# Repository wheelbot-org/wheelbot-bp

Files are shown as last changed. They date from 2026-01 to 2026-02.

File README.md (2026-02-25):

# Чертежи и 3D модели проекта wheelbot

В папке `fcstd` лежат чертежи деталей в формате FreeCAD. Каждый файл - отдельная деталь. В папке `3mf` лежат уже подготовленные для 3D печати модели. Имена файлов в папках совпадают, отличаются только разрешения.

Все чертежи адаптированы под использование подшипников от роликовых коньков - стандарт 608 (8x22x7 mm), внутренний диаметр 8 mm. Выбор обусловлен их распрастраненностью и ценой. Установка подшипников в детали предполагается запресовкой (с натягом).

Для разъемных соединений используются винты M4 цилиндрический с внутренним шестигранником и гайки к ним. Выбор обусловлен их распрастраненностью, ценой, потребностью многократной сборки и разборки, скрытие шляпки.

Список не печатных деталей по [ссылке](./EXTERNAL-PARTS.md).

## Базовые узлы

### Рама

Рама с ребрами жесткости (изгиб, кручение) - 100x200 mm, для того, чтобы деталь помещалась на столы базовых 3D принтереров. На раме сеткой 25x25 mm размещены отверстия под винты с пазами для скрытия шляпки, на обратной стороне пазы для запресовки гаек.

|  Код | Название | Описание | Файл | Превью |
|---|---|---|---|---|
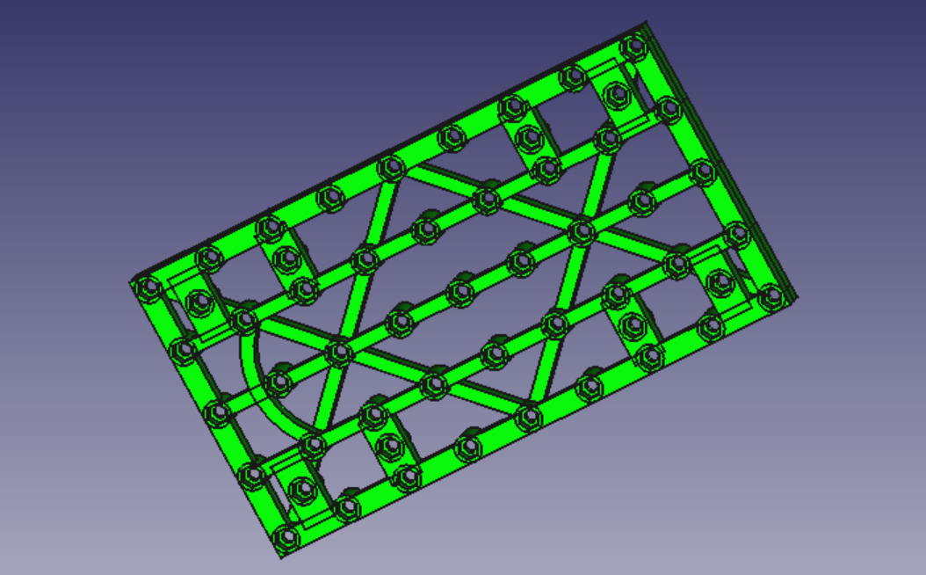
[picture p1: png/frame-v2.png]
| F.01 | Рама | Четыре площадки для крепления узлов мотор-редукторов. Одна площадка для крепления рулевого механизма на сервоприводе. | `frame-v2` |  |

### Рулевой узел

Рулевой механизим на основе сервопривода.

| Код | Название | Описание | Файл | Превью |
|---|---|---|---|---|
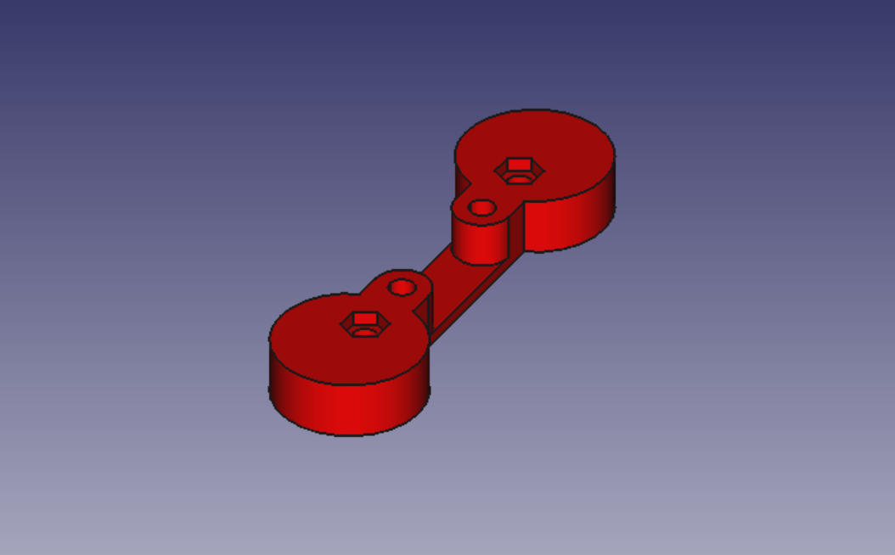
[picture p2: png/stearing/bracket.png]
| S.01 | Кронштейн-проставка | Для крепления к раме. | `stearing/bracket` |  |
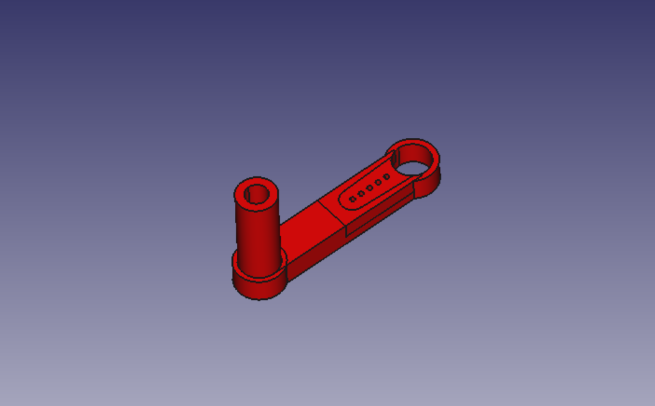
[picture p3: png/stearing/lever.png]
| S.02 | Рулевой рычаг | Передает усилие от сервопривода на центральный шатун. | `stearing/lever` |  |
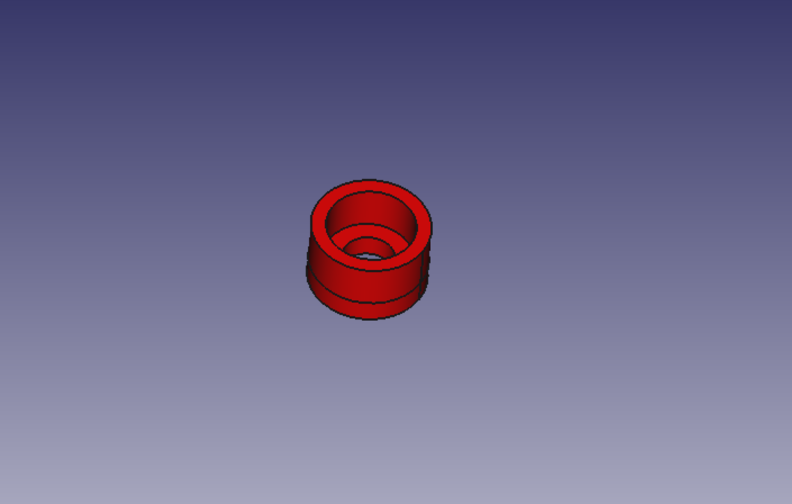
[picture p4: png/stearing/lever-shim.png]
| S.03 | Прокладки | Прокладка фиксации центрального шатуна на рулевом рычаге и боковых шатунах. Для сборки узла требуется три. | `stearing/lever-shim` |   |
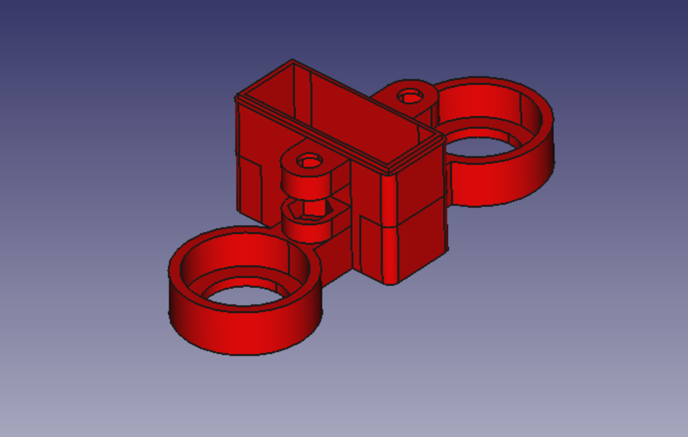
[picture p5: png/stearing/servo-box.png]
| S.04 | Корпус | Сервопривод размещается внутрь детали. Подшипники запресовываются. | `stearing/servo-box` |  |
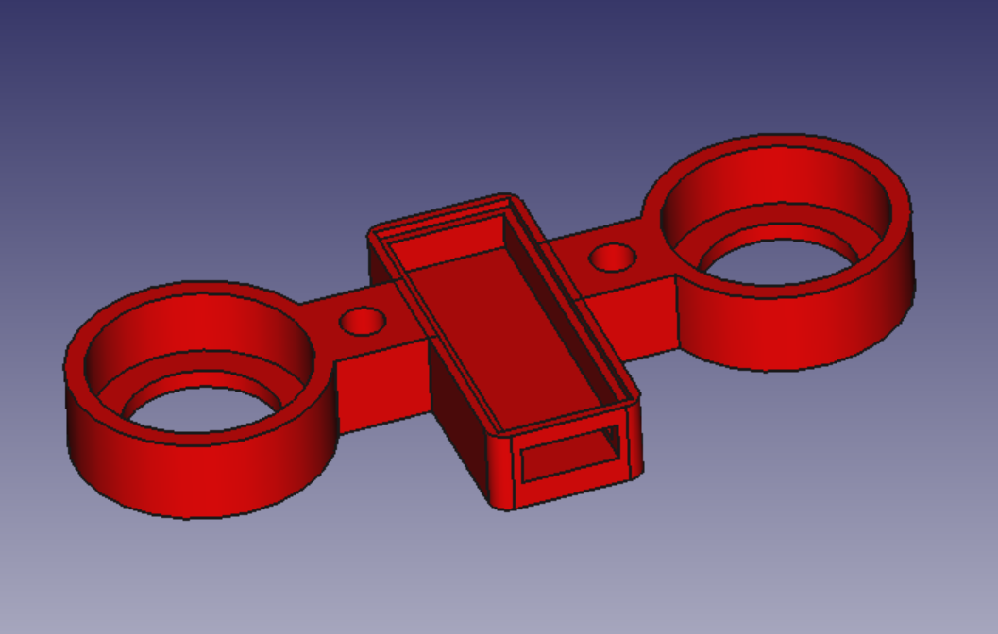
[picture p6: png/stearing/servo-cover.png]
| S.05 | Крышка | Подшипники запресовываются. | `stearing/servo-cover` |  |
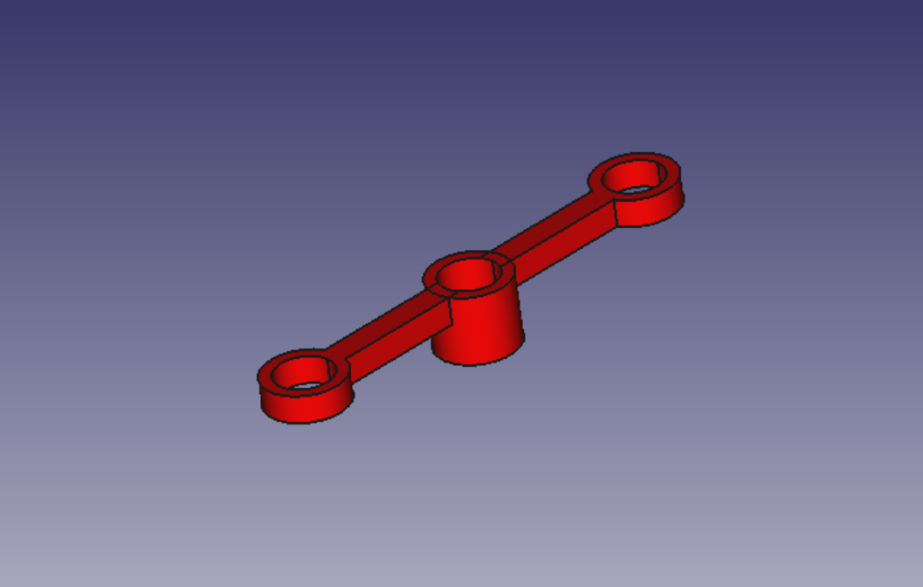
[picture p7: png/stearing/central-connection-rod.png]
| S.06 | Центральный шатун | Передает усилие на боковые шатуны. | `stearing/central-connection-rod` |  |
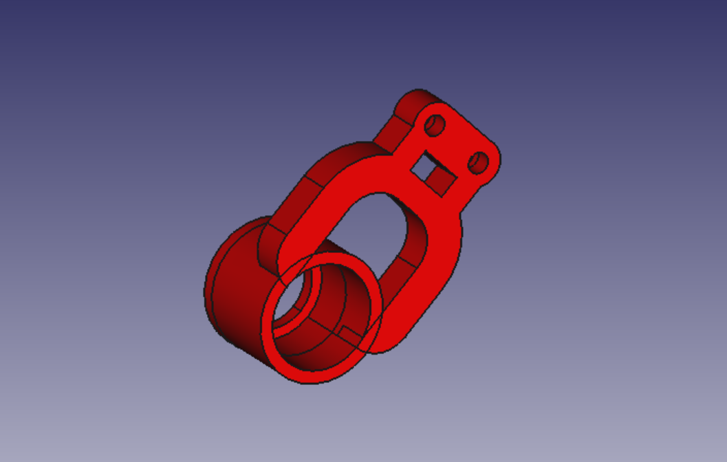
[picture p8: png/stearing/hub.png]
| S.07 | Ступицы | Для сборки узла требуется две. Деталь симетричная, зеркально отображать не нужно. | `stearing/hub` |  |
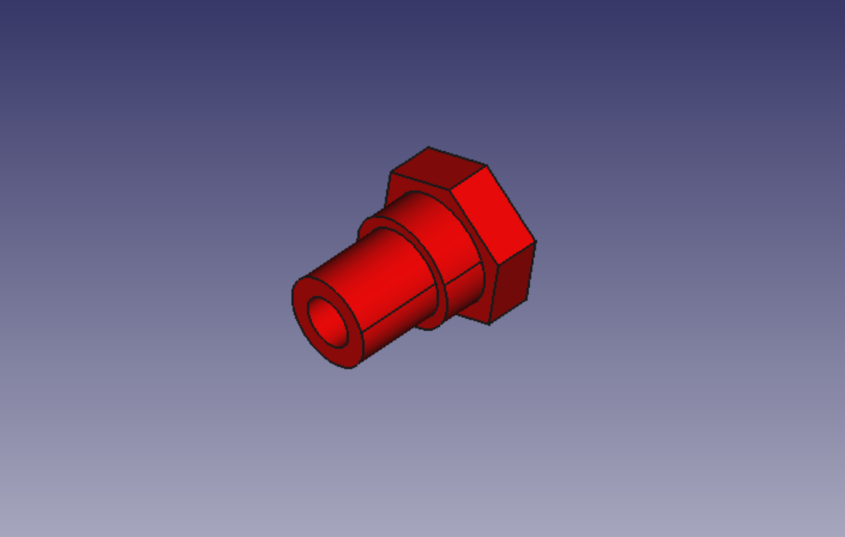
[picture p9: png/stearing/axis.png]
| S.08 | Оси | Оси для крепления дисков. Для сборки узла требуется две. | `stearing/axis` |  |
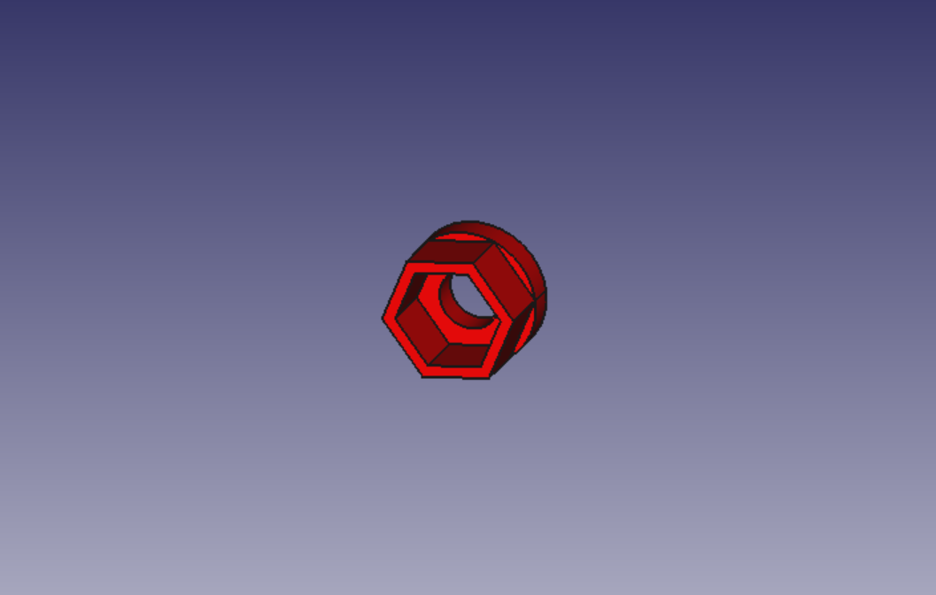
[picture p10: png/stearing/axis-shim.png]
| S.09 | Фиксаторы осей | Прокладки для фиксации подшипников к осям. Для сборки узла требуется две. | `stearing/axis-shim` |  |
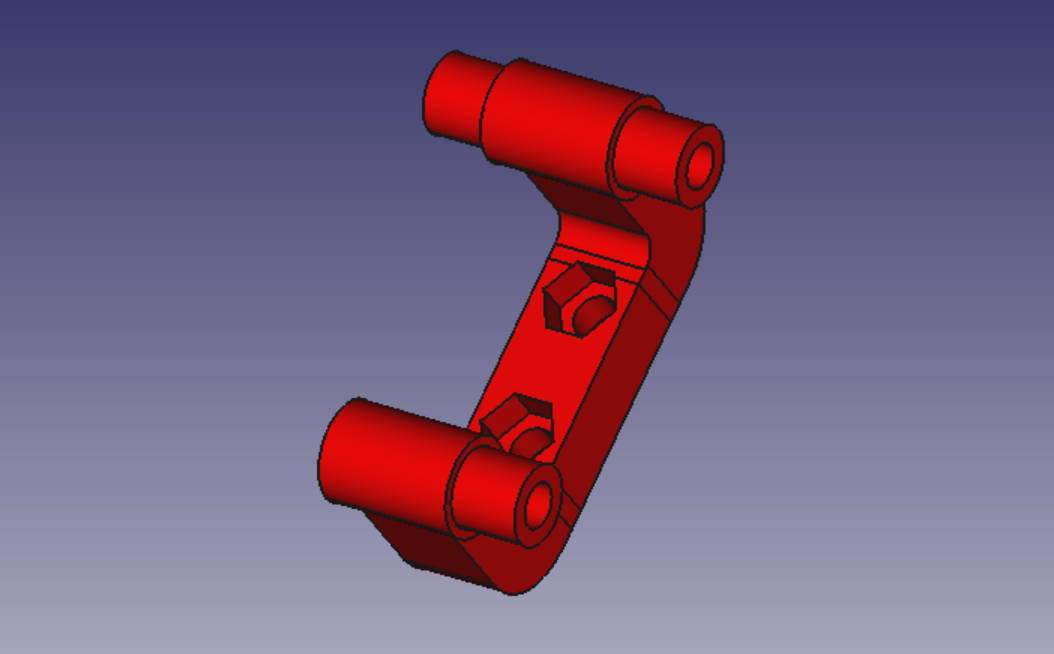
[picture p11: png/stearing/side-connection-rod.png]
| S.10 | Боковые шатуны | Передают усилие от центрального шатуна на ступицы. Для сборки узла требуется две, вторую требуется отобразить зеркально при печати. | `stearing/side-connection-rod` |  |

### Ходовой узел

Ходовые узлы построенные на мотор редукторах (DC3-6V TT). Минимум нужно два, при построении ровера без рулевого узла - четыре.

| Код | Название | Описание | Файл | Превью |
|---|---|---|---|---|
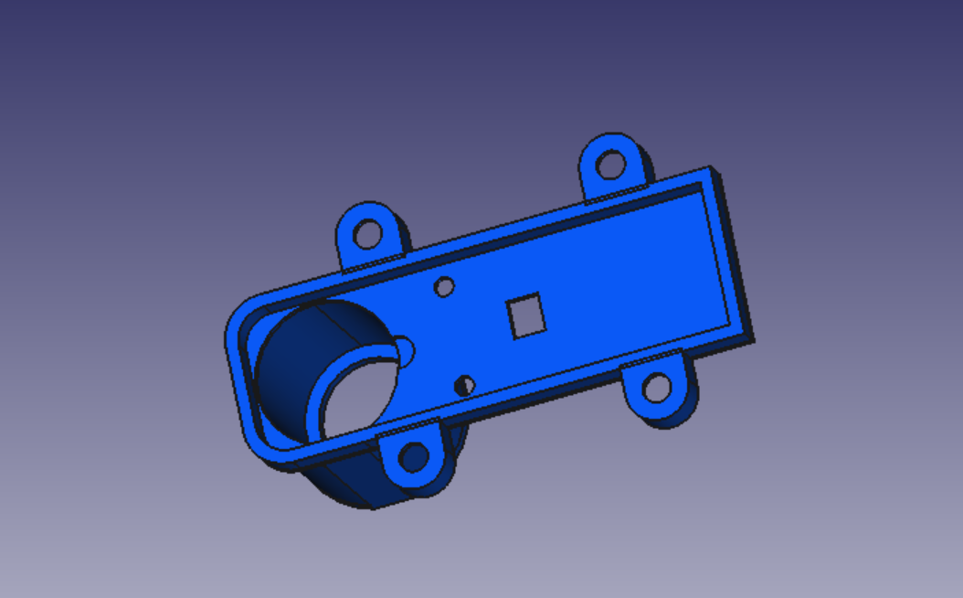
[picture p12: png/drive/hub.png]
| M.01 | Ступицы | - | `drive/hub` |  |
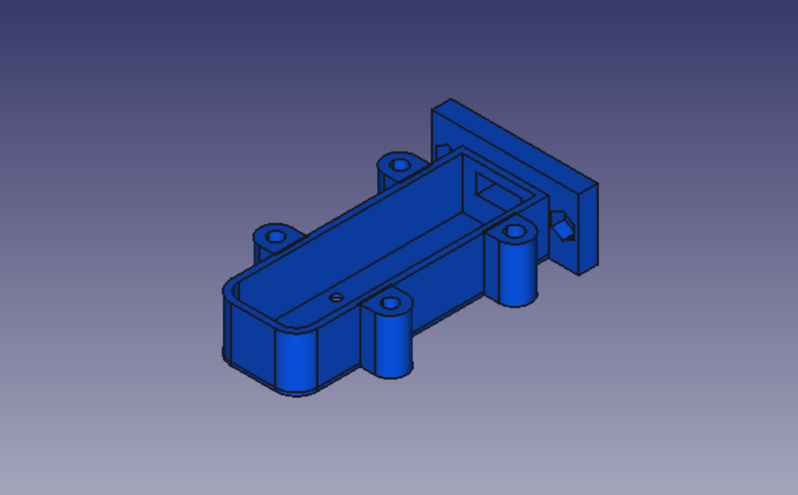
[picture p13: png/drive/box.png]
| M.02 | Корпус | Корпус для мотор-редуктора. | `drive/box` |  |
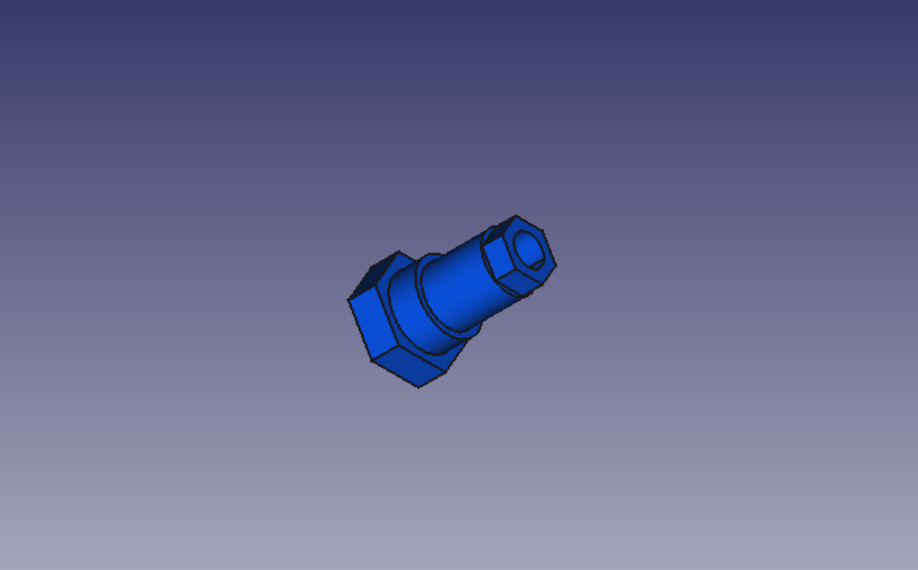
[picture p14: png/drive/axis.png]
| M.03 | Ось | - | `drive/axis` |  |
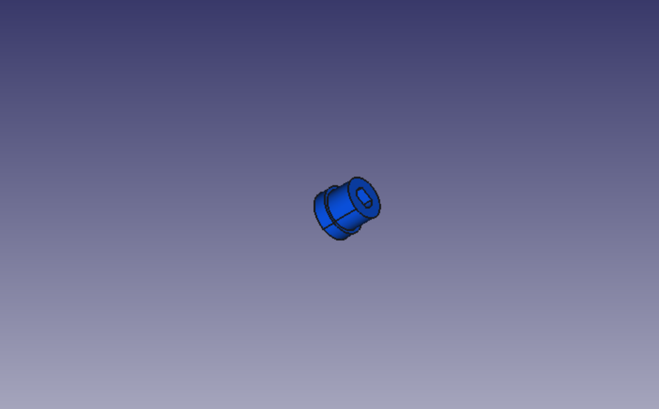
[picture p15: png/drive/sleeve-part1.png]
| M.04 | Муфта 1 | Муфта со стороны мотор-редуктора | `drive/sleeve-part1` |  |
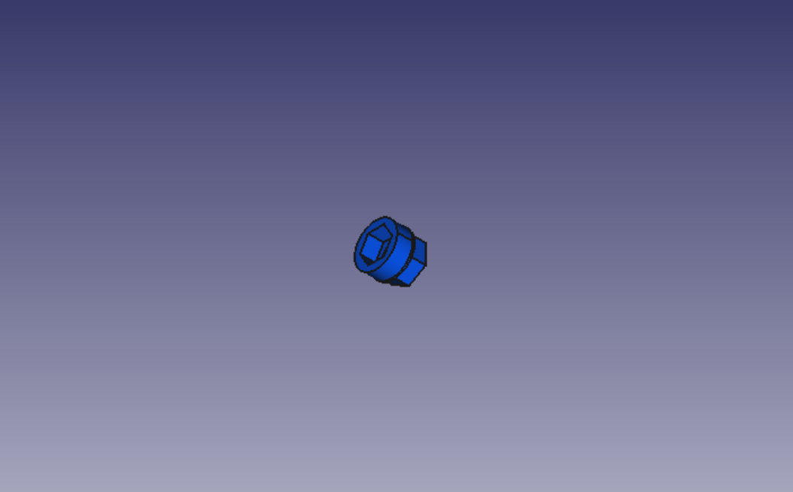
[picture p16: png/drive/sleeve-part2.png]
| M.05 | Муфта 2 | Муфта со стороны колеса | `drive/sleeve-part2` |  |

### Колесо

| Код | Название | Описание | Файл | Превью |
|---|---|---|---|---|
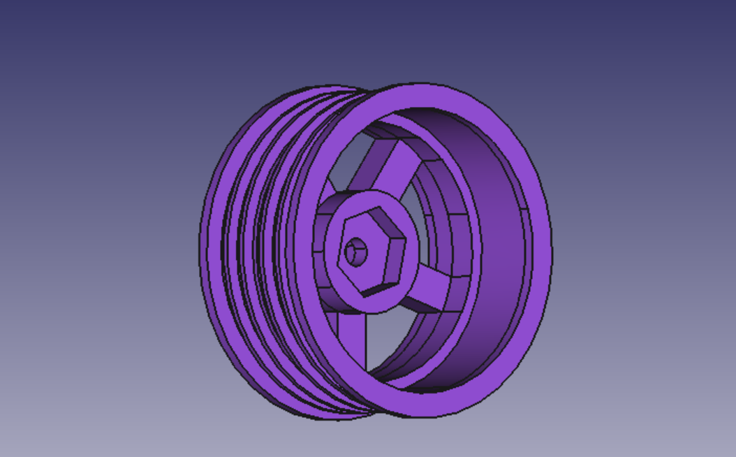
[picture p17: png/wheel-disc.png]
| W.01 | Диск | Диск для колес под покрышку для моделирования (RCAWD 1/10 63mm). Ребра на внешней стороне - необходимый элемент. | `wheel-disc` |  |

### Главный контроллер

Корпус под ESP8266 (NodeMCU), Drivers Shield.

| Код | Название | Описание | Файл | Превью |
|---|---|---|---|---|
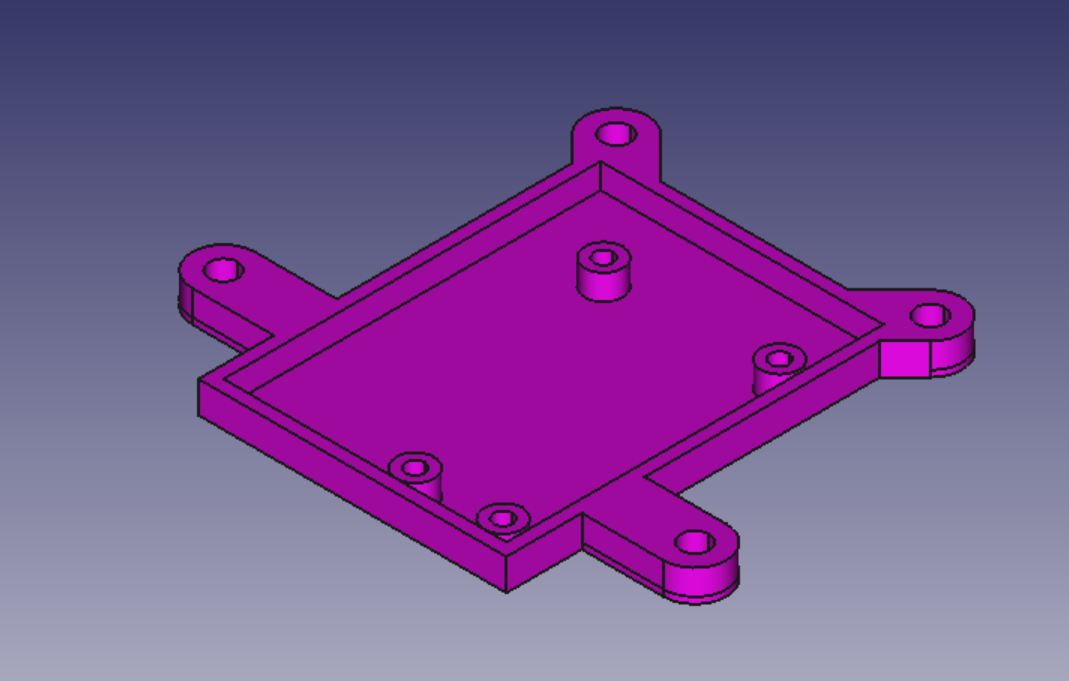
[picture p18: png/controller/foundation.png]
| MC.01 | Основание | - | `controller/foundation` |  |
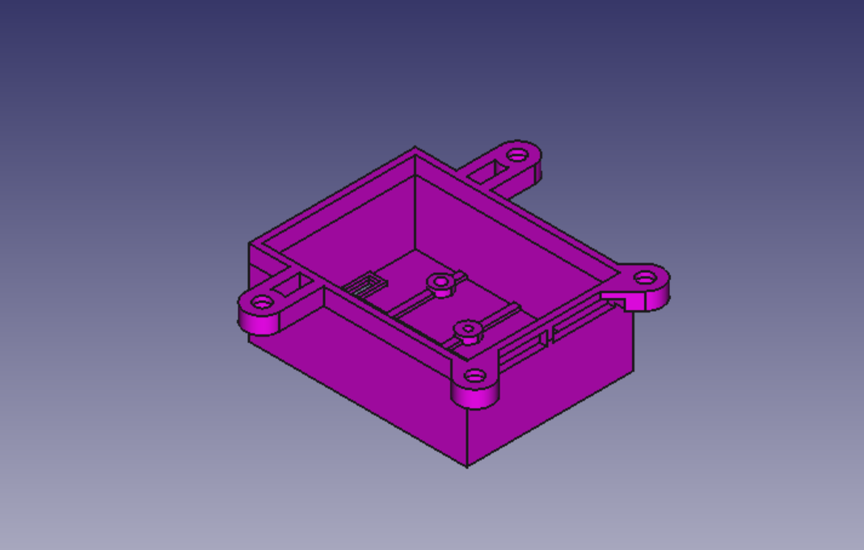
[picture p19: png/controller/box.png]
| MC.02 | Корпус | - | `controller/box` |  |

### Аккумуляторный блок

Корпус для крепления на раму батарейного отсека (ABS 18650 4x). Выполнен в 2х вариациях под BMS платы Balance и Enhance. Во всех вариантах предусмотрено крепление для ina226 и dc-dc преобразователя для питания 5 вольт.

| Код | Название | Описание | Файл | Превью |
|---|---|---|---|---|
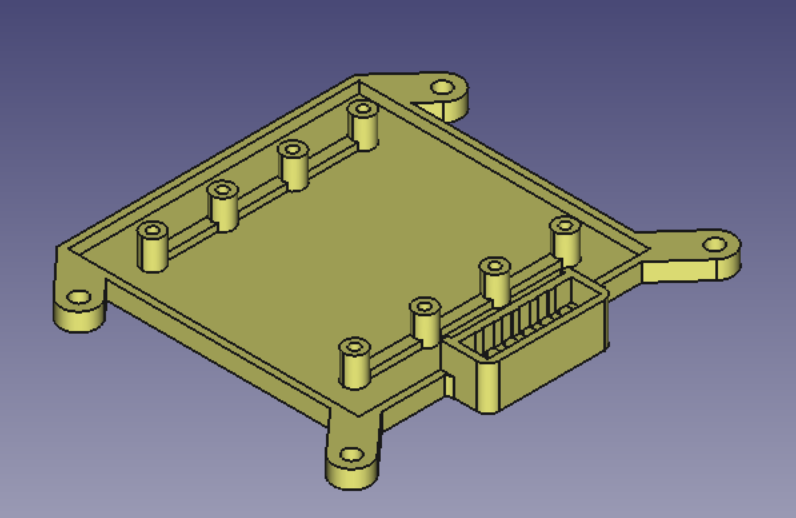
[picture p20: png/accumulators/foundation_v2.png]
| B.01 | Основание | - | `accumulators/foundation_v2` |  |
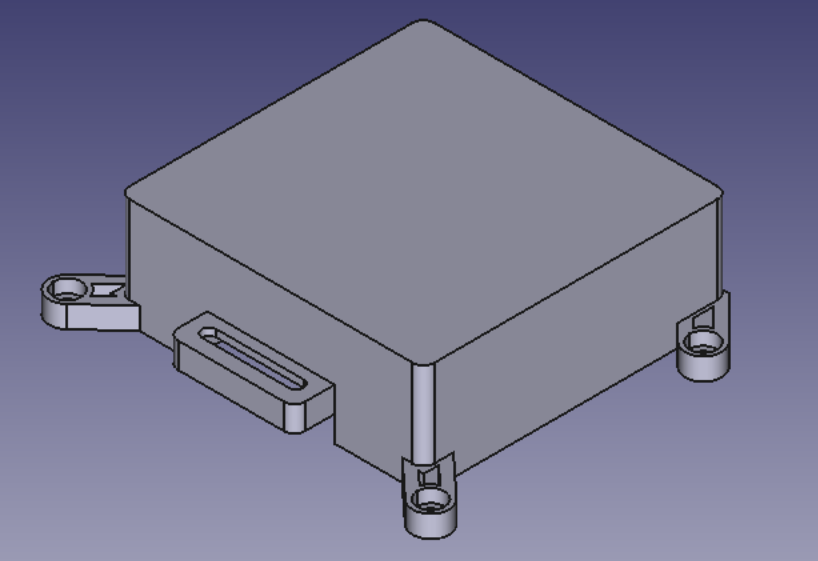
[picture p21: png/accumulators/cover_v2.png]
| B.02 | Корпус | - | `accumulators/cover_v2` |  |

## Дополнительные узлы

### Ультразвуковые дальномеры

Крепления для ультразвуковых дальномеров (HC-SR04). Жестко и противоударно прикрепляет дальномеры к раме. Прижимает шлейфы к корпусу, чтобы убрать дребезг.

| Код | Название | Описание | Файл | Превью |
|---|---|---|---|---|
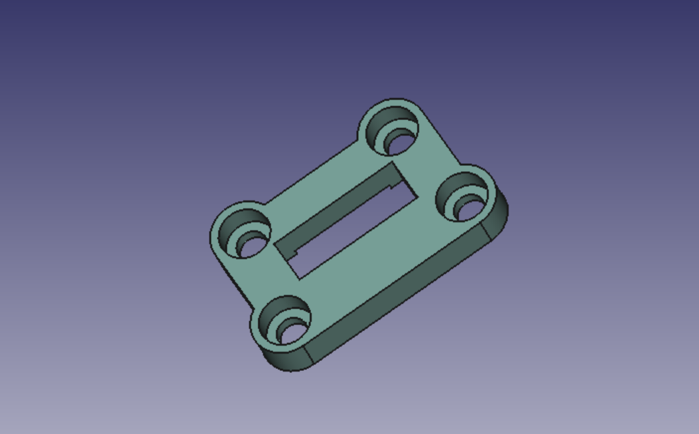
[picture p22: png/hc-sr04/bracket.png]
| US.01 | Кронштейн | Кронштейн для крепления к раме ровера. | `hc-sr04/bracket` |  |
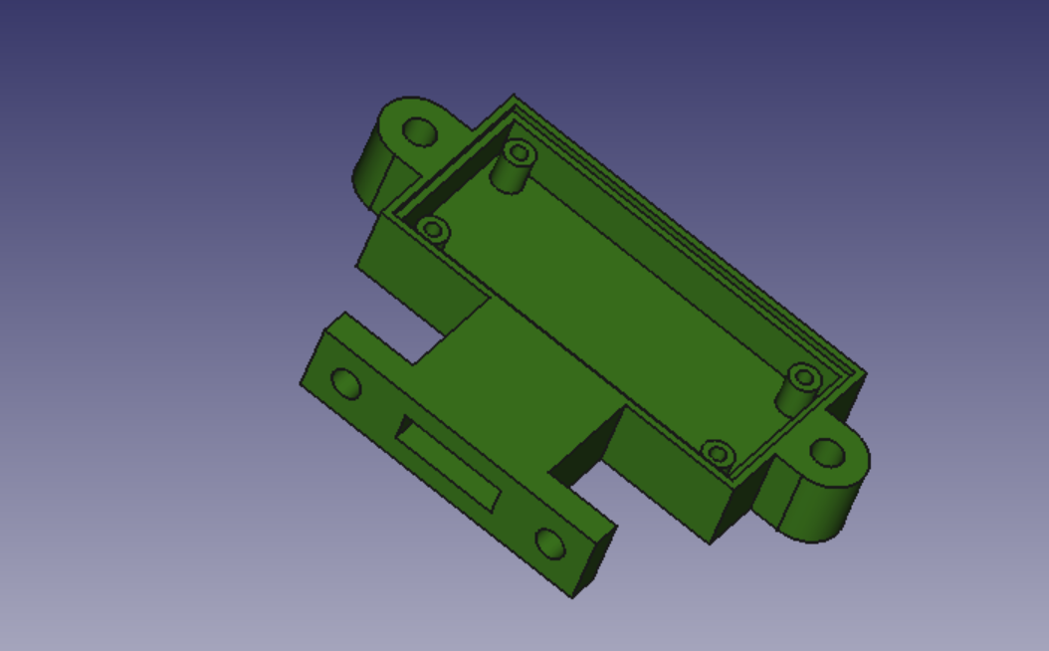
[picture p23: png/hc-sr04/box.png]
| US.02 | Корпус | - | `hc-sr04/box` |  |
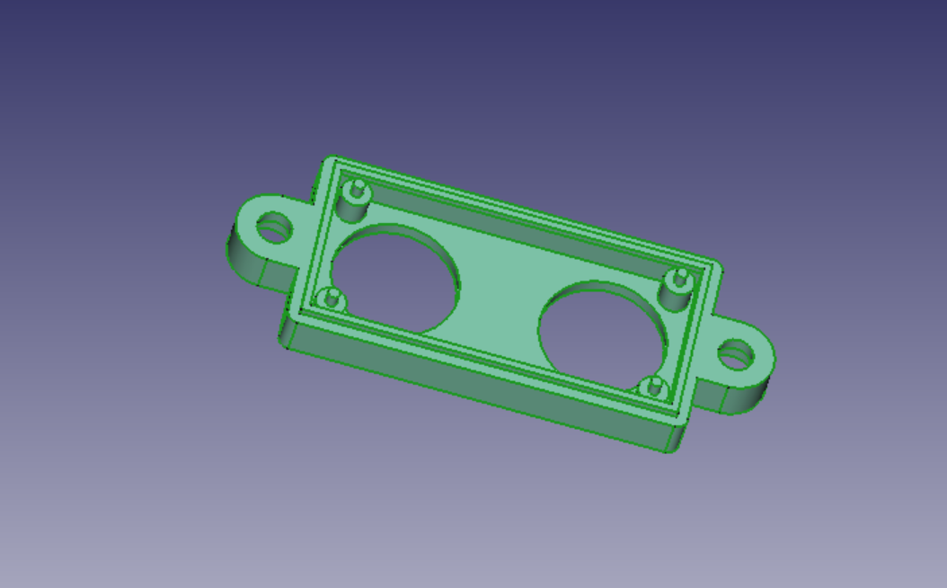
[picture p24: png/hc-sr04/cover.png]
| US.03 | Крышка | - | `hc-sr04/cover` |  |

### Цифровая камера

Крепление для цифровой камеры с контроллером (ESP32-CAM).

| Код | Название | Описание | Файл | Превью |
|---|---|---|---|---|
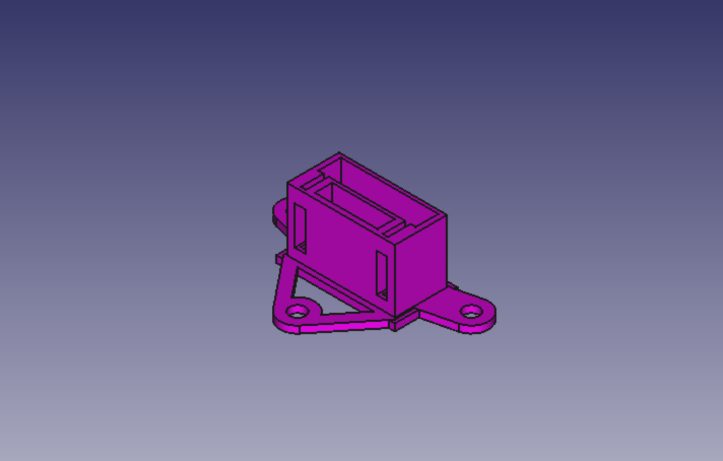
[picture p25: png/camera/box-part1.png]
| DC.01 | Основание | - | `camera/box-part1` |  |
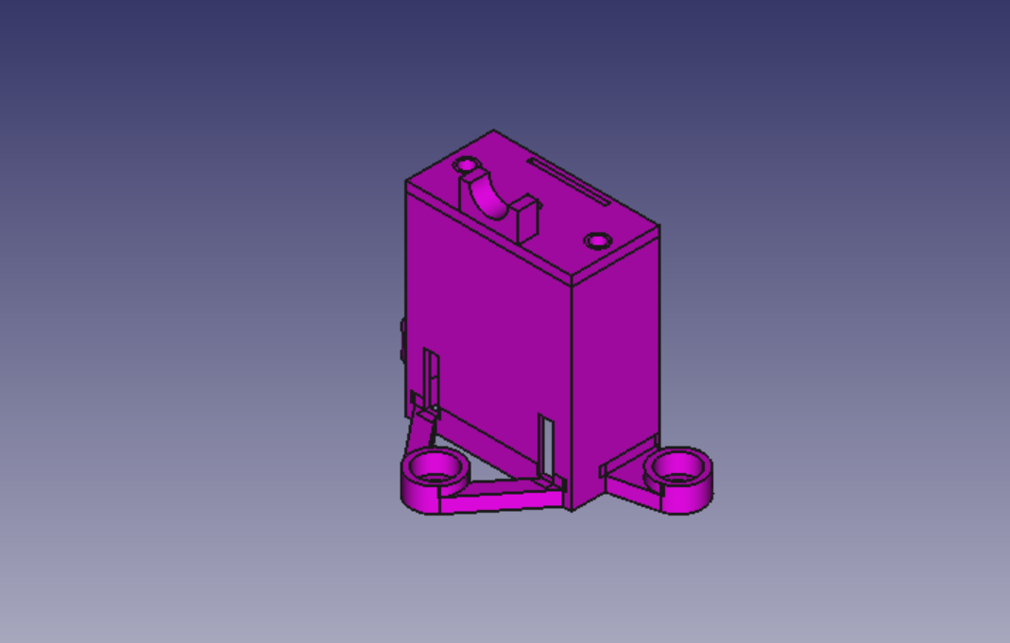
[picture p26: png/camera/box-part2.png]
| DC.02 | Корпус контроллера | - | `camera/box-part2` |  |
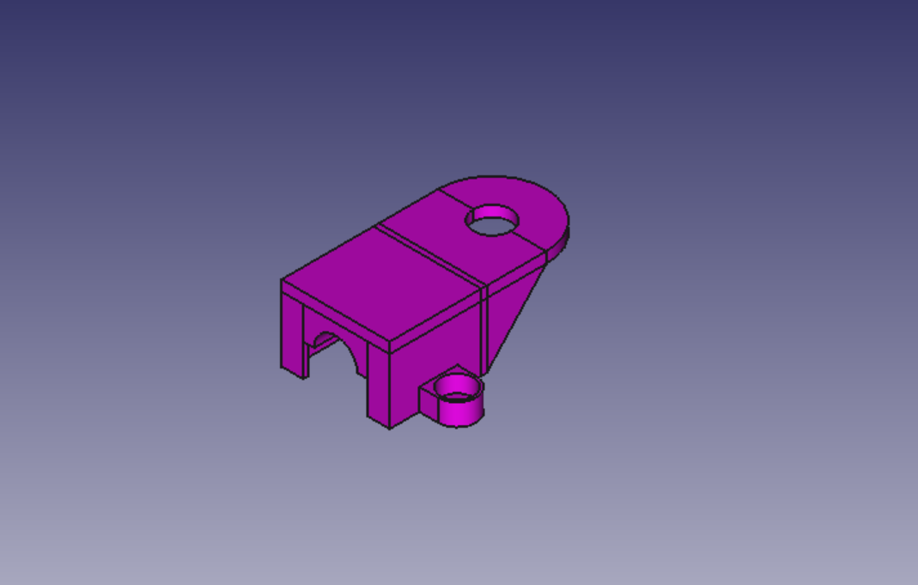
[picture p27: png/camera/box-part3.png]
| DC.03 | Корпус камеры | - | `camera/box-part3` |  |

### Инерциальный блок

Инерциальный блок на MPU6050.

| Код | Название | Описание | Файл | Превью |
|---|---|---|---|---|
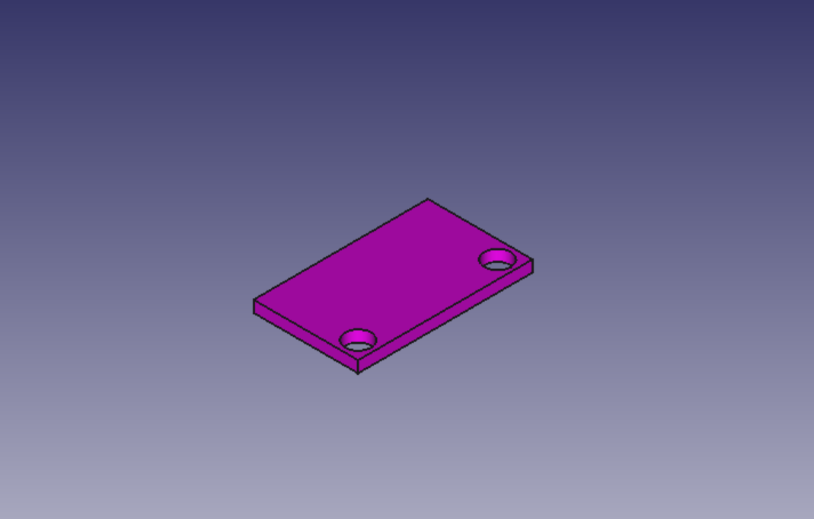
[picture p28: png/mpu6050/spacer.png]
| I.01 | Проставка | - | `mpu6050/spacer` |  |
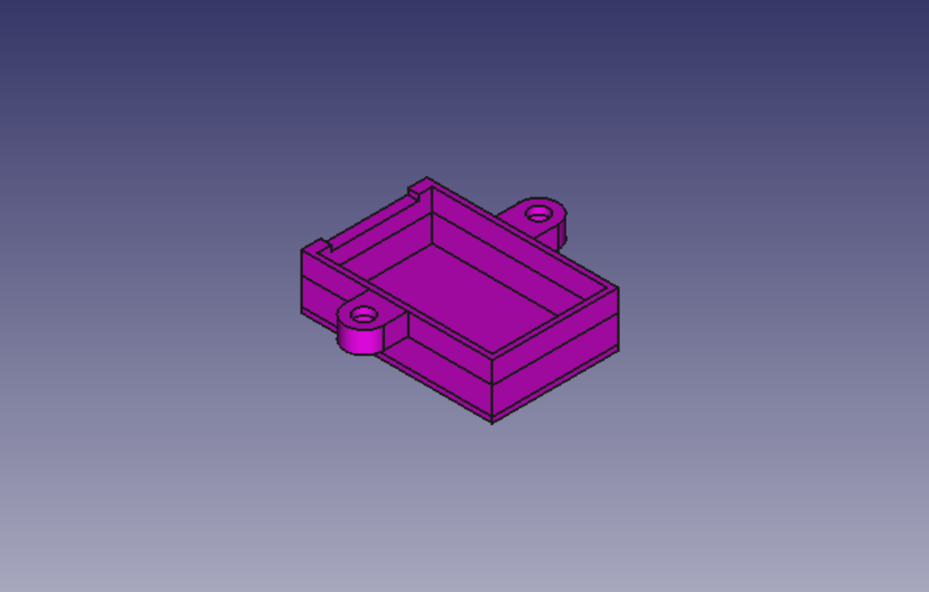
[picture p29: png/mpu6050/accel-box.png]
| I.02 | Корпус инерциального блока | - | `mpu6050/accel-box` |  |

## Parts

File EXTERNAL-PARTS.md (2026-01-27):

# Сторонние компоненты

```
TODO: 
1. Добавить винты для крепления батарейного отсека
2. Разбить болты M4 по длинне
3. Разбить болты M3 по длинне
```

Ссылки на компоненты указаны для ознакомления, не обязательно по ним можно найти самый выгодный вариант приобретения и они не являются рекомендацией продавцов. Стоимость доставки не учитывается, а стоимость самого компонента указана приблизительно на момент написания (10.12.2025). Рекомендуется искать компоненты не только в aliexpress или ozon, например инерциальных блок можно найти в 1.5 раза дешевле на специализированных сайтах.

## Базовые узлы

**Общая оценочная стоимость - 420 + 296 + 320 + 308 + 738 = 2082₽ ($26.4)**

### Рулевой узел

**Общая оценочная стоимость - 120x1 + 20x6 + 10x15 + 2x15 = 420₽ ($5.4)**

|  Код | Компонент | Описание | Количество | Цена за штуку | Ссылка |
|---|---|---|:-----:|:-----:|:---:|
| EP.01 | Сервопривод | TZT MG90S | 1 | 120 | [aliexpress](https://aliexpress.ru/item/32964755308.html?sku_id=12000041239882270) |
| EP.12 | Подшипники | 608 2RS | 6 | 20 | [aliexpress](https://aliexpress.ru/item/1005003634659574.html?sku_id=5000000008257208) |
| EP.13 | Винты M4 | цилиндрическая головка под шестигранник | 15 | 10 | [ozon](https://www.ozon.ru/product/vint-din-912-m4h25-s-tsilindricheskoy-golovkoy-20-sht-polnaya-rezba-1503319040/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) |
| EP.15 | Гайки М4 | - | 15 | 2 | [ozon](https://www.ozon.ru/product/gayka-shestigrannaya-m4-50-sht-3021665374/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) |

### Ходовой узел

Из рассчета использования в ровере 2х узлов.

**Общая оценочная стоимость - 80x2 + 20x2 + 10x8 2x8 = 296₽ ($3.8)**

|  Код | Компонент | Описание | Количество | Цена за штуку | Ссылка |
|---|---|---|:-----:|:-----:|:---:|
| EP.02 | Мотор-редуктор | TT Motor 130 DC3V-6V | 2 | 80 | [aliexpress](https://aliexpress.ru/item/1005009058317610.html?sku_id=12000047754682189) |
| EP.12 | Подшипники | 608 2RS | 2 | 20 | [aliexpress](https://aliexpress.ru/item/1005003634659574.html?sku_id=5000000008257208) |
| EP.13 | Винты M4 | цилиндрическая головка под шестигранник | 8 | 10 | [ozon](https://www.ozon.ru/product/vint-din-912-m4h25-s-tsilindricheskoy-golovkoy-20-sht-polnaya-rezba-1503319040/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) |
| EP.15 | Гайки М4 | - | 8 | 2 | [ozon](https://www.ozon.ru/product/gayka-shestigrannaya-m4-50-sht-3021665374/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) |

### Колесо

Из рассчета использования в ровере 4х узлов.

**Общая оценочная стоимость - 80x4  = 320₽ ($4.1)**

|  Код | Компонент | Описание | Количество | Цена за штуку | Ссылка |
|---|---|---|:-----:|:-----:|:---:|
| EP.11 | Шины | Резиновые шины для моделей 68 мм | 4 | 80 | [aliexpress](https://aliexpress.ru/item/1005009750617126.html?sku_id=12000050043114967) |

### Главный контроллер

**Общая оценочная стоимость - 150x1 + 70x1 + 4x10 + 4x10 + 4x2 = 308₽ ($3.9)**

|  Код | Компонент | Описание | Количество | Цена за штуку | Ссылка |
|---|---|---|:-----:|:-----:|:---:|
| EP.03 | Главный контроллер | Node MCU ESP-12E | 1 | 150 | [aliexpress](https://aliexpress.ru/item/4000124968751.html?sku_id=10000000353317935) |
| EP.04 | Плата управления двигателями | Node MCU ESP-12E Motor Shield | 1 | 70 | [aliexpress](https://aliexpress.ru/item/4000124968751.html?sku_id=10000000353317936) |
| EP.13 | Винты M4 | цилиндрическая головка под шестигранник | 4 | 10 | [ozon](https://www.ozon.ru/product/vint-din-912-m4h25-s-tsilindricheskoy-golovkoy-20-sht-polnaya-rezba-1503319040/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) |
| EP.14 | Винты M3 | цилиндрическая головка под шестигранник | 4 | 10 | [ozon](https://www.ozon.ru/product/vint-din-912-m3h6-s-tsilindricheskoy-golovkoy-20-sht-polnaya-rezba-2154074485/) |
| EP.15 | Гайки М4 | - | 4 | 2 | [ozon](https://www.ozon.ru/product/gayka-shestigrannaya-m4-50-sht-3021665374/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) |

### Аккумуляторный блок

**Общая оценочная стоимость - 150x4 + 90x1 + 10x4 + 2x4 = 738₽ ($9.4)**

|  Код | Компонент | Описание | Количество | Цена за штуку | Ссылка |
|---|---|---|:-----:|:-----:|:---:|
| EP.10 | Аккумуляторы | 18650 | 4 | 150 | [aliexpress](https://aliexpress.ru/item/32364018657.html?sku_id=64644614117) |
| EP.18 | Батарейный отсек | ABS 18650 x4 | 1 | 90 | [aliexpress](https://aliexpress.ru/item/1005003595795784.html?sku_id=12000026426467013)
| EP.13 | Винты M4 | цилиндрическая головка под шестигранник | 4 | 10 | [ozon](https://www.ozon.ru/product/vint-din-912-m4h25-s-tsilindricheskoy-golovkoy-20-sht-polnaya-rezba-1503319040/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) |
| EP.15 | Гайки М4 | - | 4 | 2 | [ozon](https://www.ozon.ru/product/gayka-shestigrannaya-m4-50-sht-3021665374/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) |

## Дополнительные узлы

### Ультразвуковые дальномеры

Из рассчета использования в ровере 2х узлов.

**Общая оценочная стоимость - 60x2 + 10x6 + 2x6  = 186₽ ($2.4)**

|  Код | Компонент | Описание | Количество | Цена за штуку | Ссылка |
|---|---|---|:-----:|:-----:|:---:|
| EP.09 | Ультразвуковой дальномер | HC-SR04 | 2 | 60 | [aliexpress](https://aliexpress.ru/item/32523466302.html?sku_id=12000018735793132) |
| EP.13 | Винты M4 | цилиндрическая головка под шестигранник | 6 | 10 | [ozon](https://www.ozon.ru/product/vint-din-912-m4h25-s-tsilindricheskoy-golovkoy-20-sht-polnaya-rezba-1503319040/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) |
| EP.15 | Гайки М4 | - | 6 | 2 | [ozon](https://www.ozon.ru/product/gayka-shestigrannaya-m4-50-sht-3021665374/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) |

### Цифровая камера

**Общая оценочная стоимость - 290x1 + 500x1 + 50x1 + 10x3 + 10x2 + 2x3 = 893₽ ($11.4)**

|  Код | Компонент | Описание | Количество | Цена за штуку | Ссылка |
|---|---|---|:-----:|:-----:|:---:|
| EP.05 | Контроллер камеры | ESP32-CAM GC2145 OV2640 | 1 | 290 | [aliexpress](https://aliexpress.ru/item/1005009722182358.html?sku_id=12000049951427476) |
| EP.06 | Камера | UICPAL OV2640 2MP | 1 | 500 | [aliexpress](https://aliexpress.ru/item/1005004578163738.html?sku_id=12000029695768804) |
| EP.08 | Wi-Fi антена | - | 1 | 50 | [aliexpress](https://aliexpress.ru/item/1005006136328251.html?sku_id=12000037925424379) |
| EP.13 | Винты M4 | цилиндрическая головка под шестигранник | 3 | 10 | [ozon](https://www.ozon.ru/product/vint-din-912-m4h25-s-tsilindricheskoy-golovkoy-20-sht-polnaya-rezba-1503319040/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) |
| EP.14 | Винты M3 | цилиндрическая головка под шестигранник | 2 | 10 | [ozon](https://www.ozon.ru/product/vint-din-912-m3h6-s-tsilindricheskoy-golovkoy-20-sht-polnaya-rezba-2154074485/) |
| EP.15 | Гайки М4 | - | 3 | 2 | [ozon](https://www.ozon.ru/product/gayka-shestigrannaya-m4-50-sht-3021665374/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) |

### Инерциальный блок

**Общая оценочная стоимость - 500x1 + 10x4 = 540₽ ($6.9)**

|  Код | Компонент | Описание | Количество | Цена за штуку | Ссылка |
|---|---|---|:-----:|:-----:|:---:|
| EP.07 | Инерциальный блок | GY-521 (MPU-6050) | 1 | 500 | [aliexpress](https://aliexpress.ru/item/1005009112378053.html?sku_id=12000047959053803) |
| EP.14 | Винты M3 | цилиндрическая головка под шестигранник | 4 | 10 | [ozon](https://www.ozon.ru/product/vint-din-912-m3h6-s-tsilindricheskoy-golovkoy-20-sht-polnaya-rezba-2154074485/) |

## Общий список сторонних компонентов

|  Код | Компонент | Описание | Количество | Цена за штуку | Ссылка |
|---|---|---|:-----:|:-----:|:---:|
| EP.01 | Сервопривод | TZT MG90S | 1 | 120 | [aliexpress](https://aliexpress.ru/item/32964755308.html?sku_id=12000041239882270) |
| EP.02 | Мотор-редуктор | TT Motor 130 DC3V-6V | 2 | 80 | [aliexpress](https://aliexpress.ru/item/1005009058317610.html?sku_id=12000047754682189) |
| EP.03 | Главный контроллер | Node MCU V3 | 1 | 150 | [aliexpress](https://aliexpress.ru/item/4000124968751.html?sku_id=10000000353317935) |
| EP.04 | Плата управления двигателями | Node MCU V3 Motor Shield | 1 | 70 | [aliexpress](https://aliexpress.ru/item/4000124968751.html?sku_id=10000000353317936) |
| EP.05 | Контроллер камеры | ESP32-CAM GC2145 OV2640 | 1 | 290 | [aliexpress](https://aliexpress.ru/item/1005009722182358.html?sku_id=12000049951427476) |
| EP.06 | Камера | UICPAL OV2640 2MP | 1 | 500 | [aliexpress](https://aliexpress.ru/item/1005004578163738.html?sku_id=12000029695768804) |
| EP.07 | Инерциальный блок | GY-521 (MPU-6050) | 1 | 500 | [aliexpress](https://aliexpress.ru/item/1005009112378053.html?sku_id=12000047959053803) |
| EP.08 | Wi-Fi антена | - | 1 | 50 | [aliexpress](https://aliexpress.ru/item/1005006136328251.html?sku_id=12000037925424379) |
| EP.09 | Ультразвуковой дальномер | HC-SR04 | 2 | 60 | [aliexpress](https://aliexpress.ru/item/32523466302.html?sku_id=12000018735793132) |
| EP.10 | Аккумуляторы | 18650 | 4 | 170 | [aliexpress](https://aliexpress.ru/item/32364018657.html?sku_id=64644614117) |
| EP.11 | Шины | Tamiya XV01 XV02 TT01 TT02 | 4 | 80 | [aliexpress](https://aliexpress.ru/item/1005009750617126.html?sku_id=12000050043114967) |
| EP.12 | Подшипники | 608 2RS | 8 | 20 | [aliexpress](https://aliexpress.ru/item/1005003634659574.html?sku_id=5000000008257208) |
| EP.13 | Винты M4 | цилиндрическая головка под шестигранник | 46 | 10 | [ozon](https://www.ozon.ru/product/vint-din-912-m4h25-s-tsilindricheskoy-golovkoy-20-sht-polnaya-rezba-1503319040/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) |
| EP.14 | Винты M3 | цилиндрическая головка под шестигранник | 10 | 10 | [ozon](https://www.ozon.ru/product/vint-din-912-m3h6-s-tsilindricheskoy-golovkoy-20-sht-polnaya-rezba-2154074485/) |
| EP.15 | Гайки М4 | - | ? | 2 | [ozon](https://www.ozon.ru/product/gayka-shestigrannaya-m4-50-sht-3021665374/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) |
| EP.16 | Шлейфы | 10 pin 1 метр | 1 | 158 | [ozon](https://www.ozon.ru/product/shleyf-10-pin-shag-1-27-mm-1-metr-2859960506/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) |
| EP.17 | Провод | медный многопроволочный 4х жильный | 1 | 175 | [ozon](https://www.ozon.ru/product/provod-soedinitelnyy-pvs-4h0-75-mm2-belyy-med-gost-1-metr-1109352394/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) |
| EP.18 | Батарейный отсек | ABS 18650 x4 | 1 | 90 | [aliexpress](https://aliexpress.ru/item/1005003595795784.html?sku_id=12000026426467013)

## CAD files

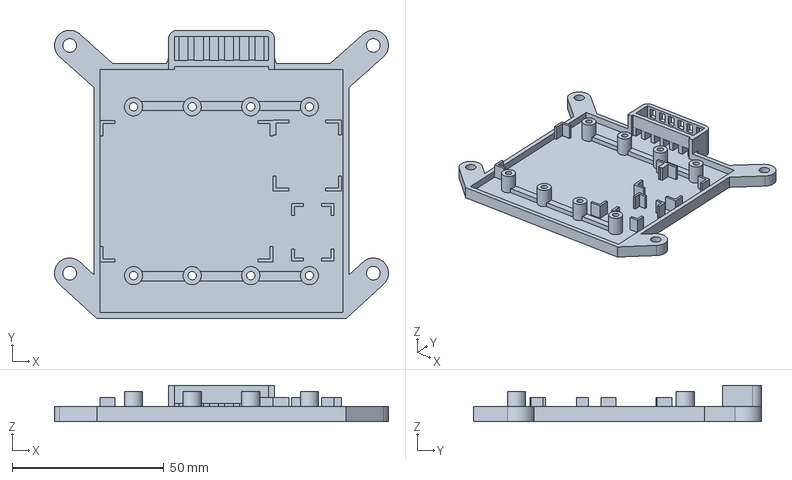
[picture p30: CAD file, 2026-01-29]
fcstd/accumulators/foundation_v2.fcstd
110.0 x 95.0 x 12.0 mm

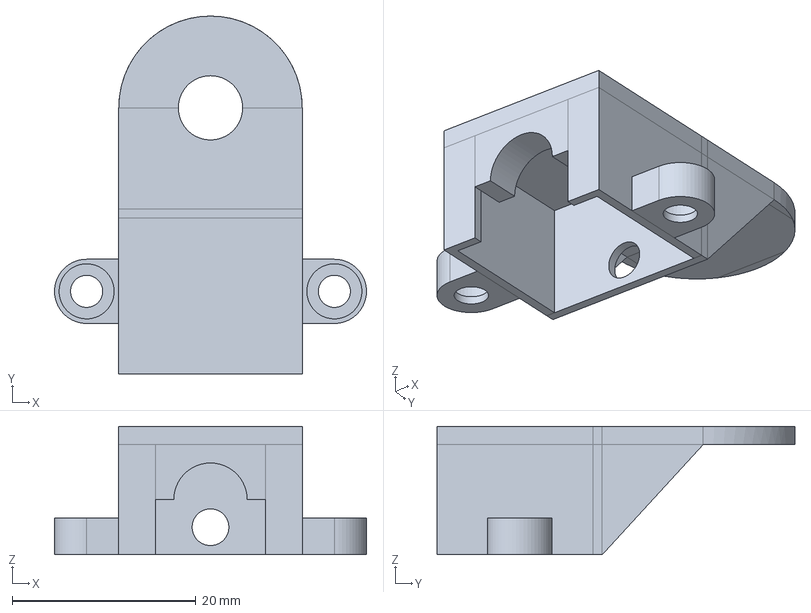
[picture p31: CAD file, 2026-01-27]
fcstd/camera/box-part3.fcstd
34.0 x 39.0 x 14.0 mm

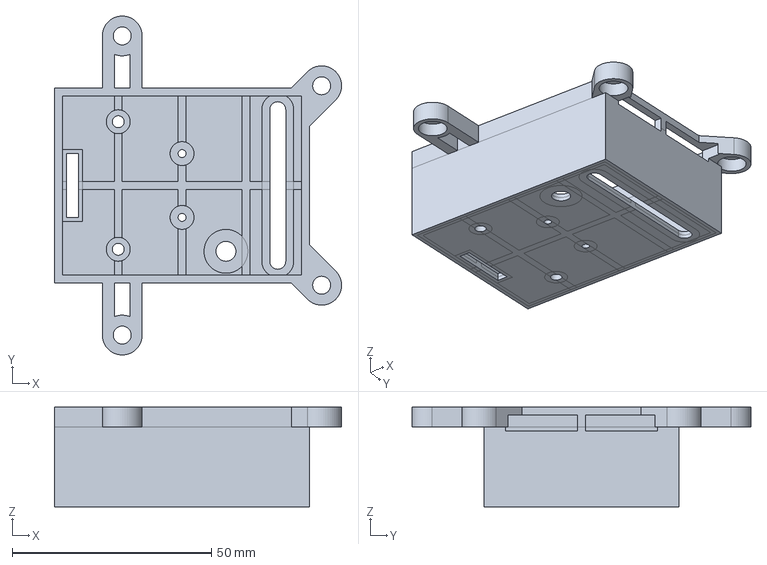
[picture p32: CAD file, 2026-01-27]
fcstd/controller/box.fcstd
72.0 x 85.0 x 25.0 mm

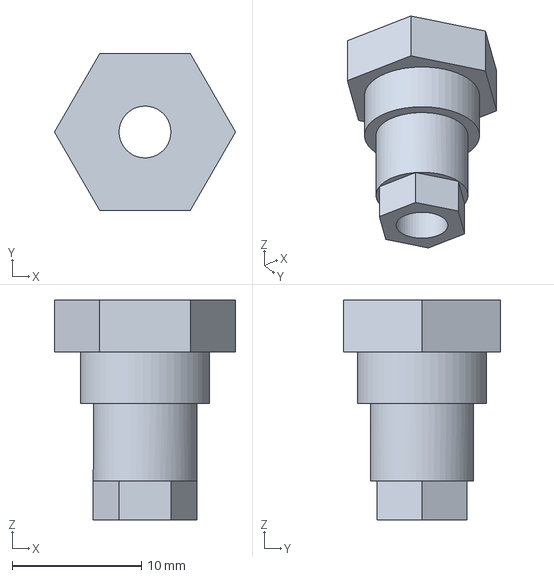
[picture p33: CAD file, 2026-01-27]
fcstd/drive/axis.fcstd
14.0 x 12.1 x 17.0 mm

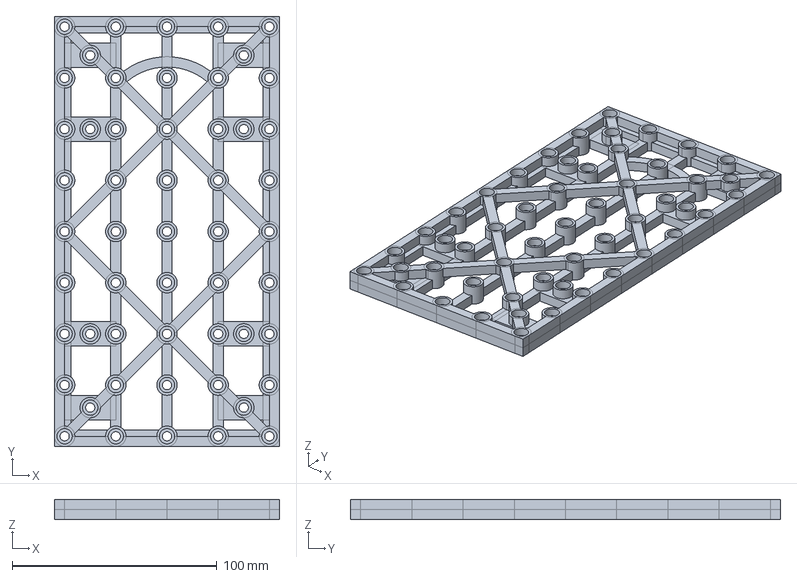
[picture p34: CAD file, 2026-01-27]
fcstd/frame-v2.fcstd
110.0 x 210.0 x 10.0 mm

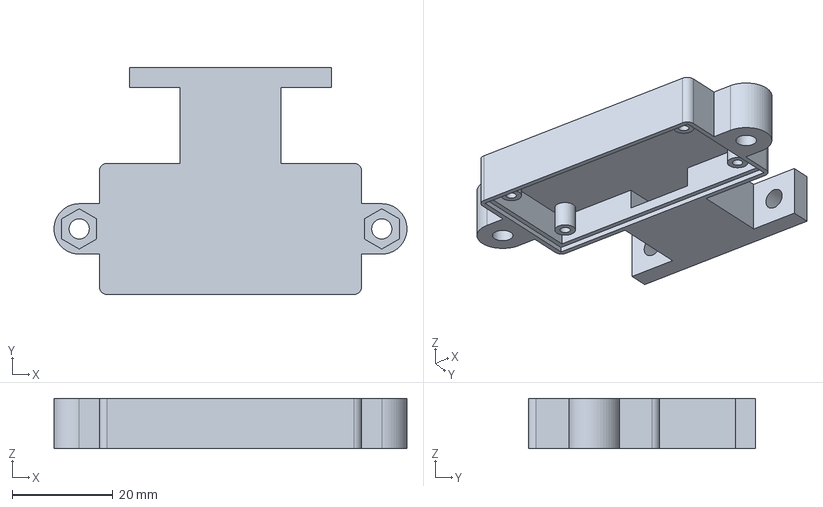
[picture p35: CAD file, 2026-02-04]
fcstd/hc-sr04/box.fcstd
70.0 x 45.0 x 10.0 mm

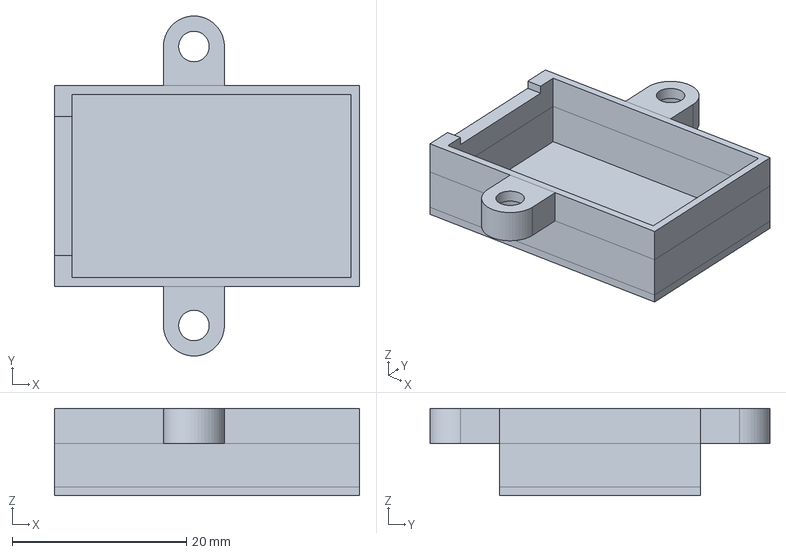
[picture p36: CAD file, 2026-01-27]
fcstd/mpu6050/accel-box.fcstd
35.0 x 39.0 x 10.0 mm

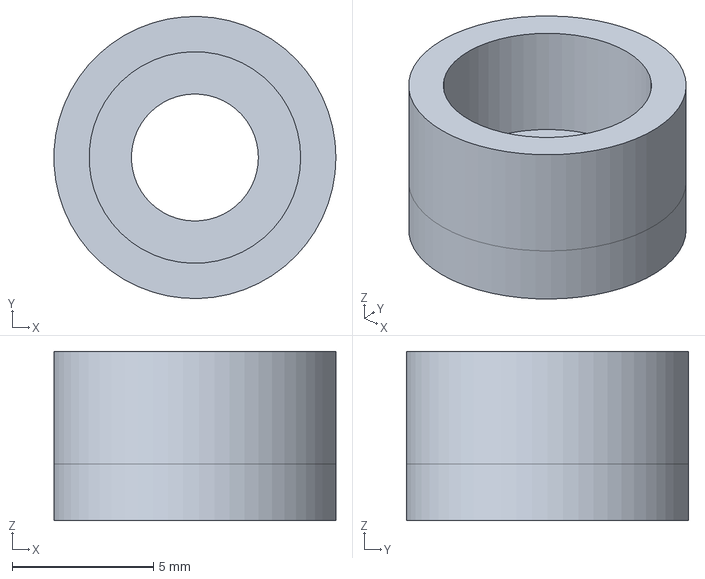
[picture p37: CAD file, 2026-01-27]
fcstd/stearing/lever-shim.fcstd
9.99 x 10.00 x 6.00 mm

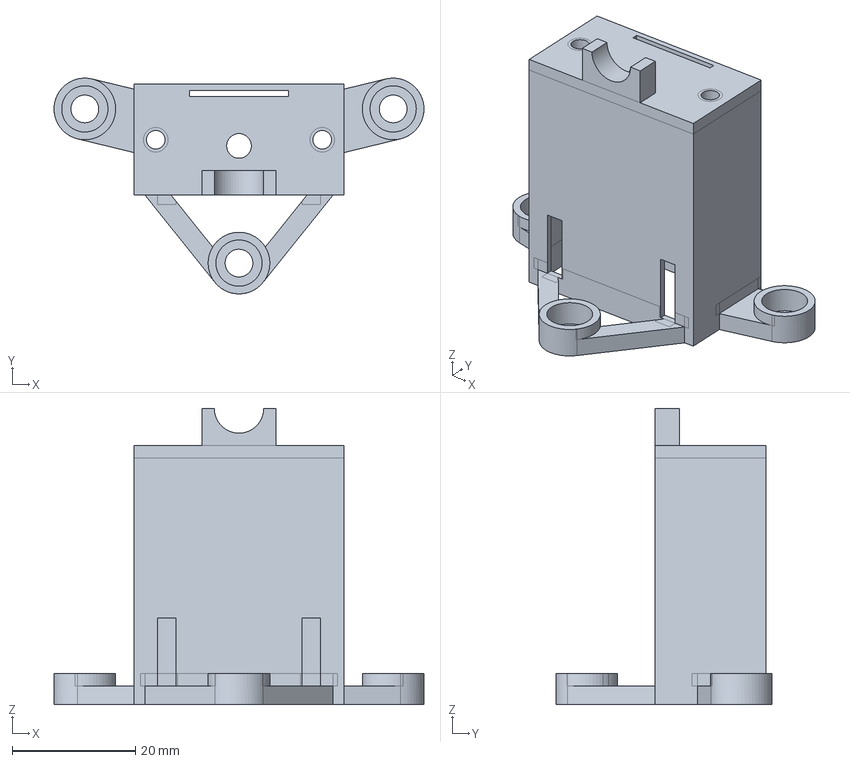
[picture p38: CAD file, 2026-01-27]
fcstd/camera/box-part2.fcstd
60.0 x 35.0 x 48.0 mm

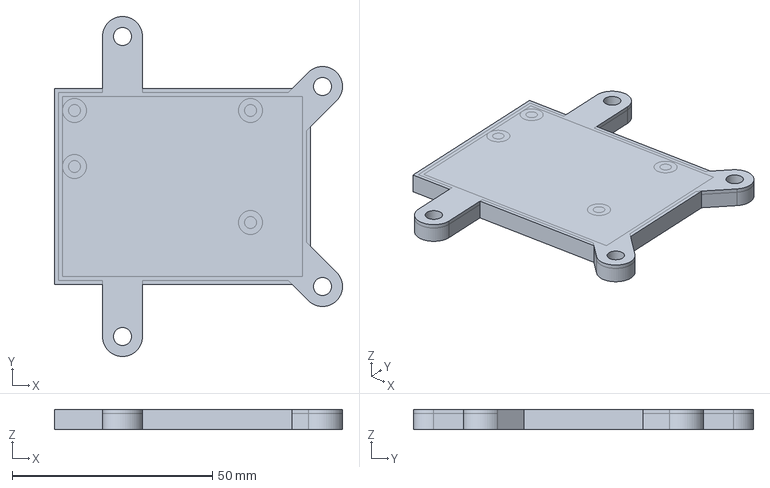
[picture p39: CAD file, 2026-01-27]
fcstd/controller/foundation.fcstd
72.0 x 85.0 x 5.00 mm

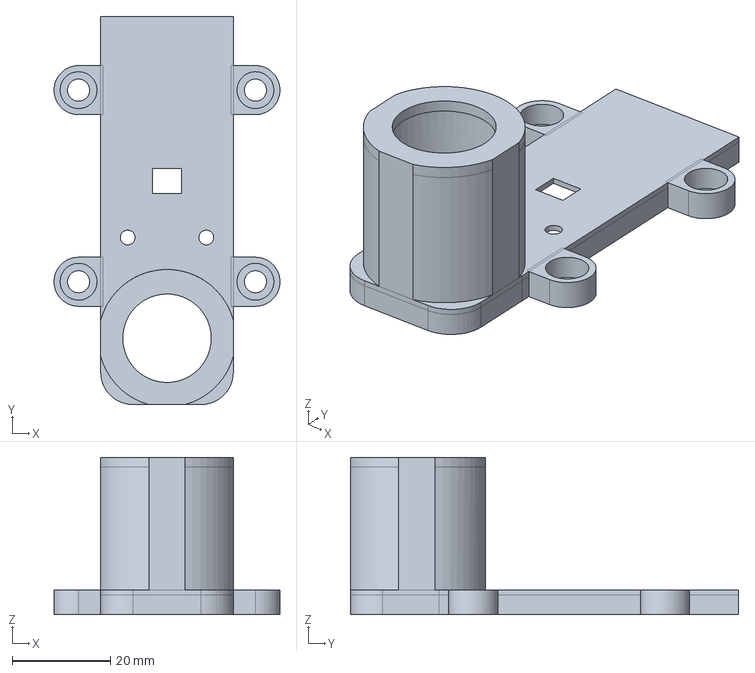
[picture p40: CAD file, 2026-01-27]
fcstd/drive/hub.fcstd
46.0 x 79.0 x 32.0 mm

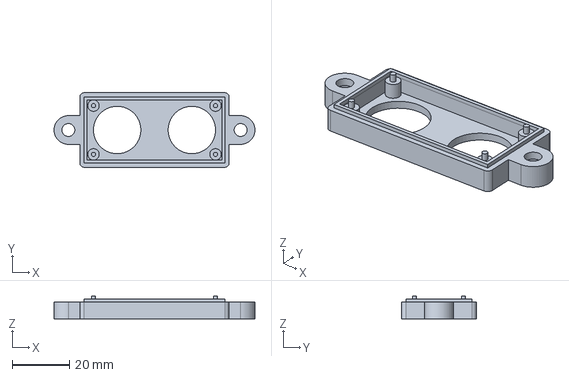
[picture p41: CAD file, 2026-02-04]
fcstd/hc-sr04/cover.fcstd
70.0 x 26.0 x 8.00 mm

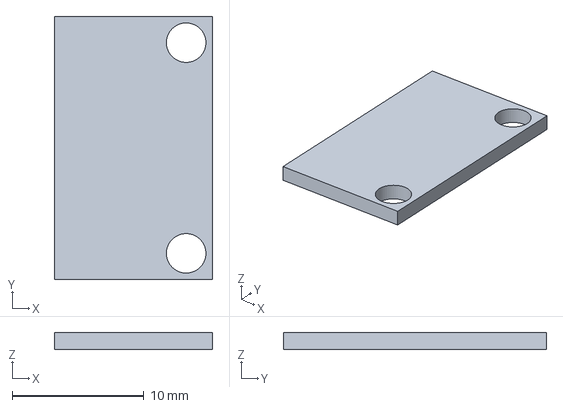
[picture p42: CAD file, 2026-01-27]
fcstd/mpu6050/spacer.fcstd
12.0 x 20.0 x 1.30 mm

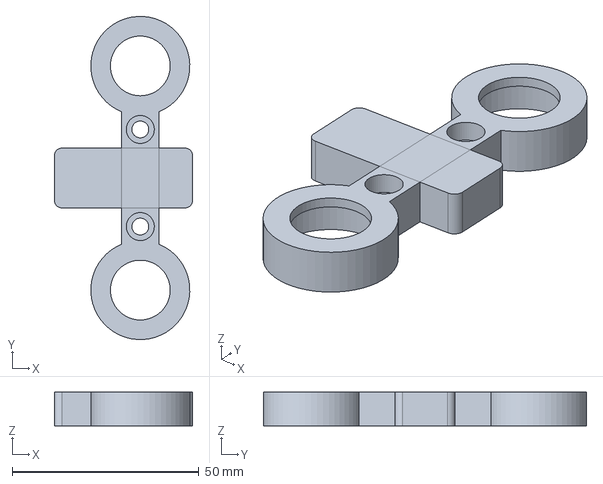
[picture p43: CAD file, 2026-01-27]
fcstd/stearing/servo-cover.fcstd
37.0 x 86.5 x 9.00 mm

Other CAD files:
fcstd/accumulators/foundation_balansed_v2.fcstd
fcstd/wheel-disc.fcstd
fcstd/accumulators/cover_balansed_v2.fcstd
fcstd/camera/box-part1.fcstd
3mf/accumulators/box.3mf
3mf/accumulators/cover_balansed_v2.3mf
3mf/accumulators/cover_v2.3mf
3mf/accumulators/foundation.3mf
3mf/accumulators/foundation_balansed_v2.3mf
3mf/accumulators/foundation_v2.3mf
3mf/camera/box-part1.3mf
3mf/camera/box-part2.3mf
3mf/camera/box-part3.3mf
3mf/controller/box.3mf
3mf/controller/foundation.3mf
3mf/drive/axis.3mf
3mf/drive/box.3mf
3mf/drive/hub.3mf
3mf/drive/sleeve-part1.3mf
3mf/drive/sleeve-part2.3mf
3mf/frame-v2.3mf
3mf/hc-sr04/box.3mf
3mf/hc-sr04/bracket.3mf
3mf/hc-sr04/cover.3mf
3mf/mpu6050/accel-box.3mf
3mf/mpu6050/spacer.3mf
3mf/stearing/axis-shim.3mf
3mf/stearing/axis.3mf
3mf/stearing/bracket.3mf
3mf/stearing/central-connection-rod.3mf
3mf/stearing/hub.3mf
3mf/stearing/lever-shim.3mf
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

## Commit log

2026-01-29 Fix accumulators box (BMS Enhanced)
    [cover_balansed_v2.3mf, cover_balansed_v2.fcstd, cover_v2.3mf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]
2026-01-29 Fix accumulators box (BMS Balanced)
    [cover_balansed_v2.3mf, cover_balansed_v2.fcstd, foundation_balansed_v2.3mf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]
2026-02-04 Fix hc-sr04 box
    [box.3mf, box.fcstd, cover.3mf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]
2026-02-25 Add power block description
